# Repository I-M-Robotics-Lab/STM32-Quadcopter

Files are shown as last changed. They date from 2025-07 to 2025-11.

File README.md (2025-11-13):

# STM32-Quadcopter: Low-cost Quadcopter Design

### Description





**[Website](https://www.imroboticslab.com/releases)** | **[Documentation](https://www.imroboticslab.com/docs/stm32-quadcopter)**  | **[Community Discord](https://discord.com/invite/WJuUWsy6DJ)** | **[3D Models & Prints](https://makerworld.com/en/models/1695470-quadcopter-3d-printable-stm32-mcu#profileId-1797658)**

This is a quadcopter design based on the STM32F411CEU Blackpill flight controller. The flight controller is compatible with INAV 6.0 firmware. The flight controller uses an MPU6500 for inertial measurements and a BMP280 for altitude sensing, and also supports an optional GPS and magnetometer module.

The frame is composed mostly of 2D parts cut from carbon-fiber sheets. Alternatively, you can 3D-print parts in carbon-fiber-reinforced filaments (PET-CF, PAHT-CF, PA6-CF, PPS-CF), with less-critical components in ABS.

|  |
| --- |

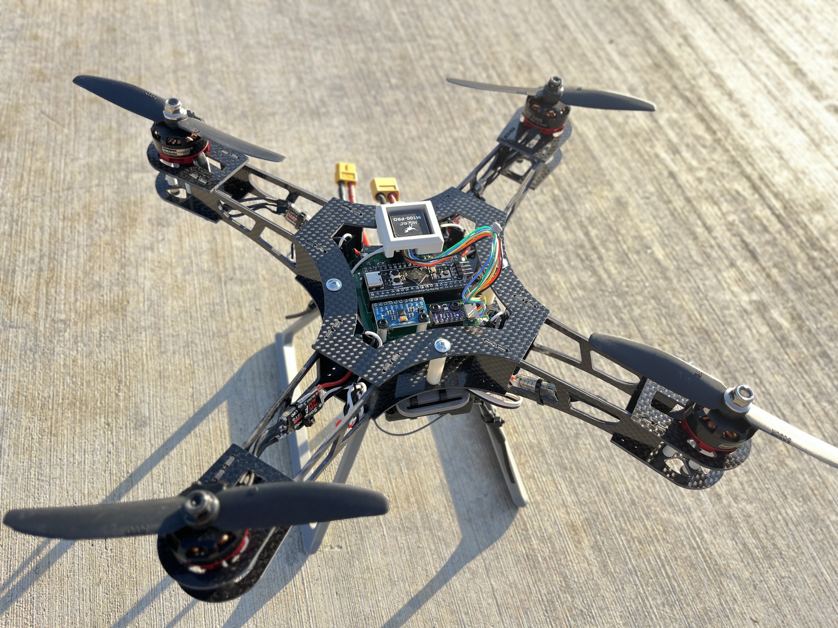
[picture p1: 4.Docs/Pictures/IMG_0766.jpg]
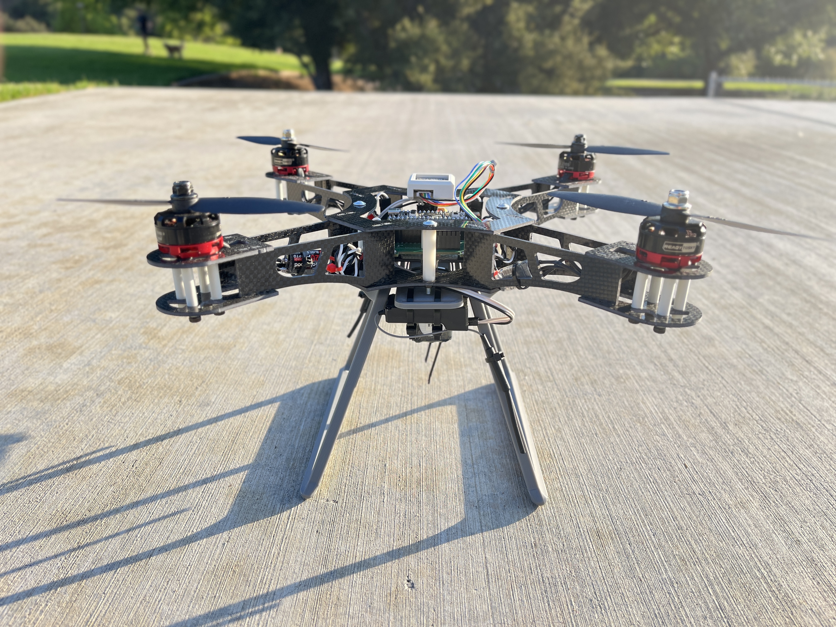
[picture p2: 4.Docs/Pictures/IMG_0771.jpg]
|  |  |
| --- | --- |

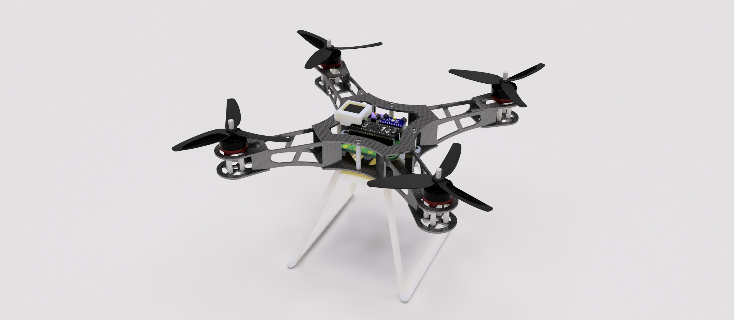
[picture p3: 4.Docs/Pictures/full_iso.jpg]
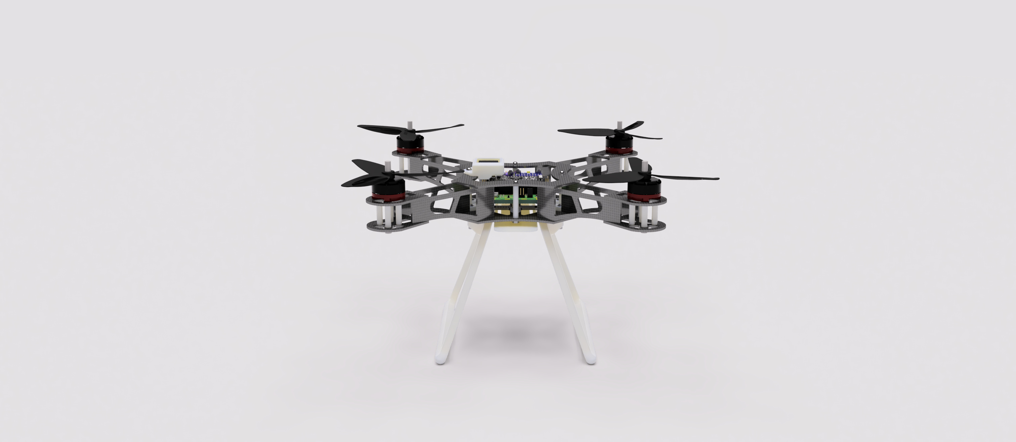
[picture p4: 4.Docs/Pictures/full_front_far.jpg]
Front view of frame
|  |  |
| --- | --- |

---

## Table of Contents

- [Introduction](#stm32-quadcopter-low-cost-quadcopter-design)
- [Frame](#frame)
  - [CF Components](#cf-components)
  - [ABS Components](#abs-components)
  - [Mechanical Components BOM](#mechanical-components-bom)
- [Electronics](#electronics)
  - [Electronics BOM](#electronics-bom)
  - [SMD Components](#smd-components)
  - [Pins](#pins)
  - [Sample Diagram](#sample-diagram)
  - [GPS (UART1) Wiring](#gps-uart1-wiring)
  - [Capacitor for Spike Filtering](#capacitor-for-spike-filtering)
- [Firmware](#firmware)
  - [Build](#build)
    - [Prerequisites](#prerequisites)
    - [Clone INAV](#clone-inav)
    - [Add Target](#add-target)
    - [Patch Code](#patch-code)
    - [Build](#build-1)
  - [Flash](#flash)
  - [MPU9250 Issue](#mpu9250-issue)
- [Configuration and Setting Up](#configuration-and-setting-up)

---

## Frame

Use the assembled CAD model in the `3.Models/` folder as a reference to build.

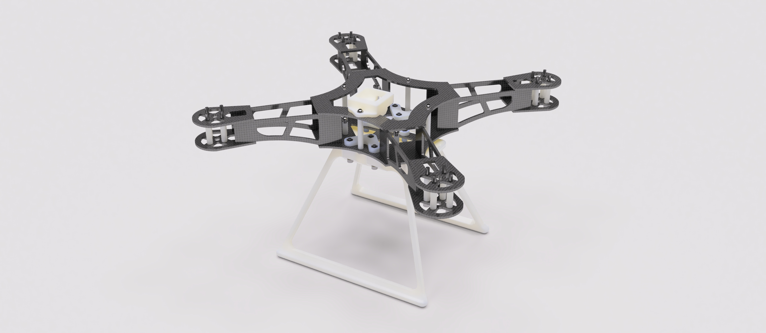
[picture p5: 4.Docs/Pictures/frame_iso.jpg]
Front view of frame


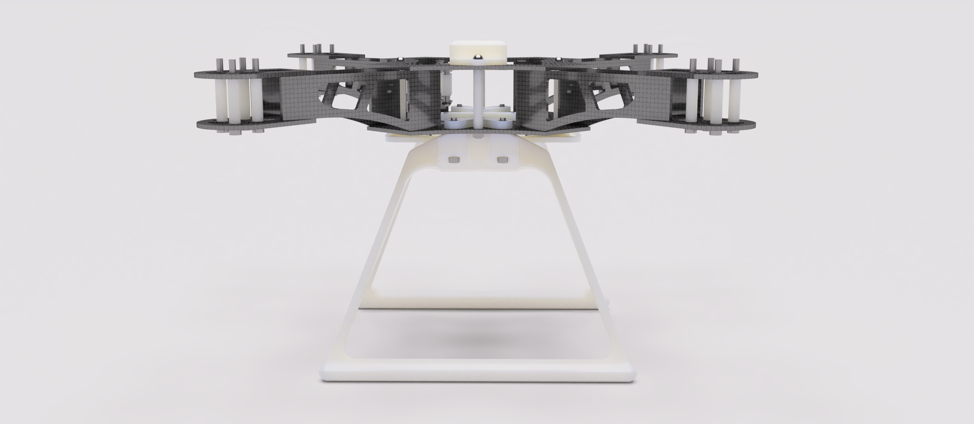
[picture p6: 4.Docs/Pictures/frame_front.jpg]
Front view of frame


### CF Components

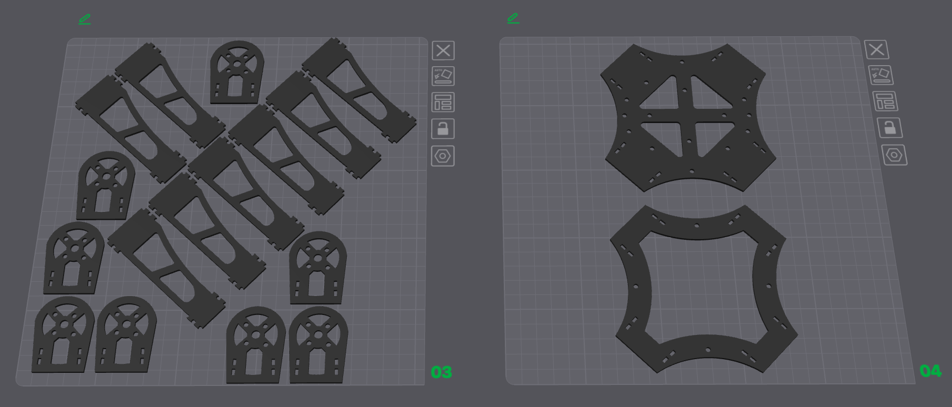
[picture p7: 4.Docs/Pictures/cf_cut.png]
CF cut patterns


*All files are under `3.Models/`. Add dogbones and tolerances for manufacturability.*

### ABS Components

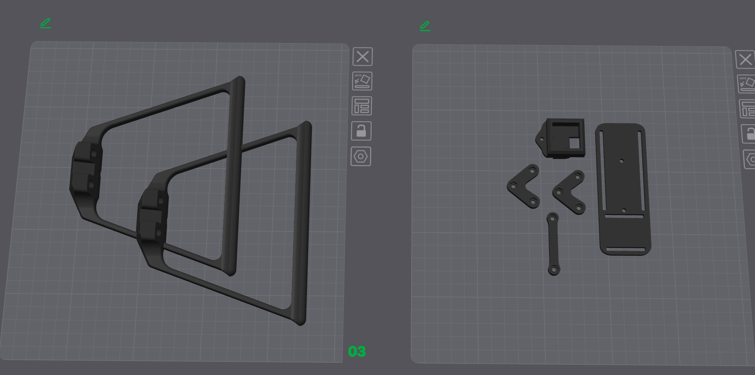
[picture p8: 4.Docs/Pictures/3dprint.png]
3D-printed ABS parts


*Recommend using a 0.4 mm or 0.6 mm high-strength print profile.*

**Mechanical Components BOM**

| Item Name | Qty |
|---|-----|
| M3 Hex Nut | 19  |
| M3 x 12mm Button Head Bolt | 2 |
| M3 x 20mm Button Head Bolt | 7 |
| M3 x 20mm Socket Head Bolt | 6 |
| M3 x 30mm Socket Head Bolt | 16  |
| M3 x 35mm Button Head Bolt | 3 |
| M3 x 40mm Button Head Bolt | 1 |
| Nylon Spacer 3-5-11.2 | 8 |
| Nylon Spacer 3-5-20 | 16  |
| Nylon Spacer 3-5-30 | 4 |
| Nylon Spacer 3-5-5 | 2 |

---
## Electronics

**Structure**
```text
1. Electronics/
  ├── Extra/
  │   ├── *.step
  │   └── ...
  ├── Hardware-backups/
  │   └── ...
  ├── Production/           ← Gerber output for fabrication
  │   ├── Hardware-B_Cu.gbl
  │   └── ...
  ├── Hardware.kicad_pcb    ← KiCAD PCB file
  ├── Hardware.kicad_sch    ← KiCAD Schematics file
  ├── Hardware.kicad_pro    ← KiCAD project
  ├── JLCPCB.kicad_dru      ← Rules for JLCPCB manufacturing
  ├── Production.zip        ← Gerber
  └── Schematics.pdf        ← Schematics
```

### Electronics BOM

| Component | Qty |
|---|:---:|
| RS2205 BLDC Motor | 4 |
| BLHeli_S 20A ESC | 4 |
| 5030R Propeller | 2 |
| STM32F411CEU6 “Blackpill” | 1 |
| MPU6500 / MPU9250 Module | 1 |
| BMP280 Module | 1 |
| 330 µF @ 50 V Capacitor | 1 |
| FS-iA6B Receiver | 1 |
| FS-iA6B Transmitter | 1 |
| Ovonic 1500 mAh 120C 3s Battery | 1 |
| XT60 Connector | 1 |

### SMD Components

Gerber files and BOM are available under the electronics folder.

### Pins

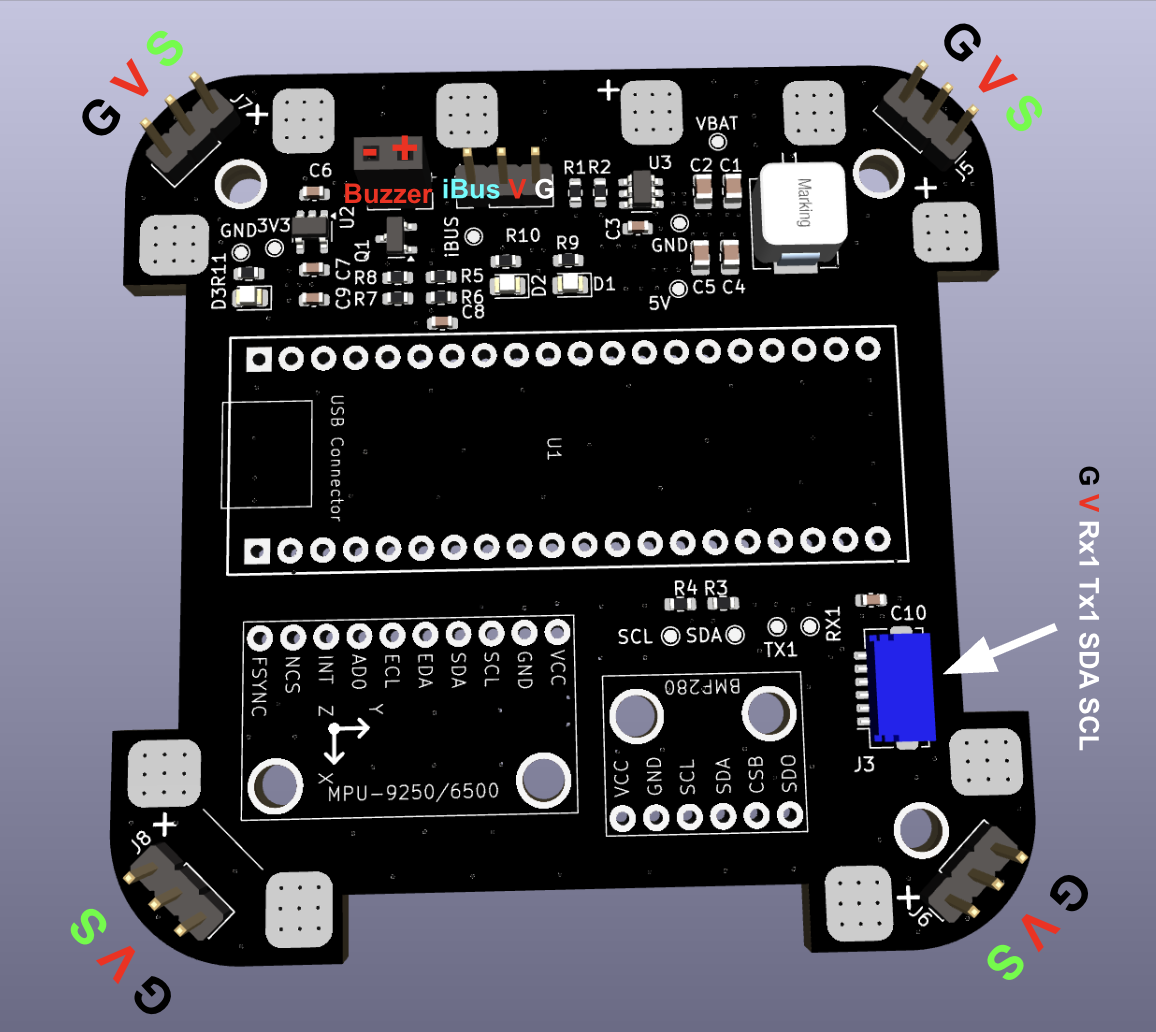
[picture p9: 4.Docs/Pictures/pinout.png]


### Sample Diagram

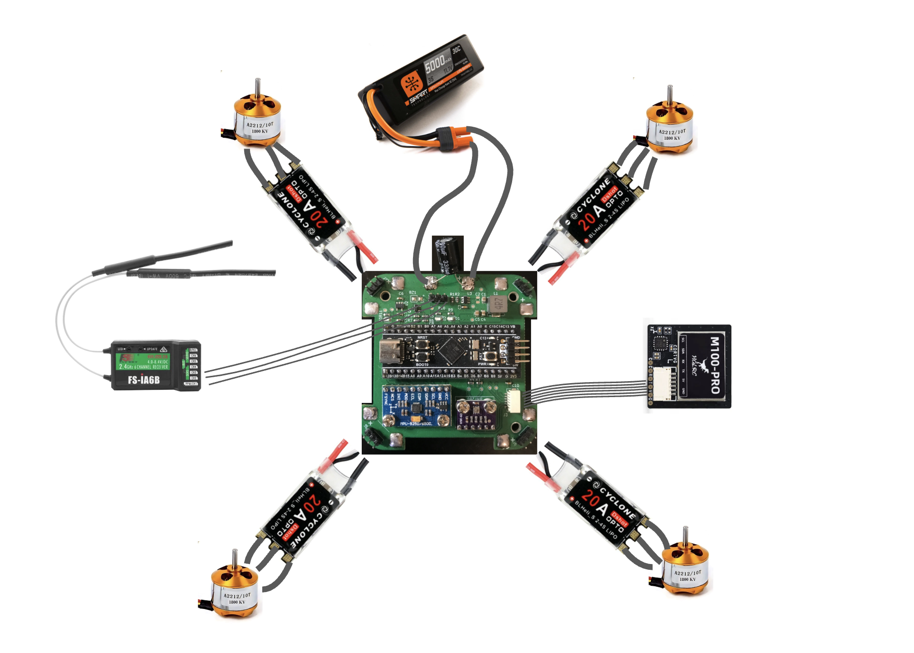
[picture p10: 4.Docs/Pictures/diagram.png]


*Diagram only; not actual wiring. Please follow the strict pin assignments.*

### GPS (UART1) Wiring

Ensure connectors are wired correctly according to the pinout. Note that RX should connect to TX: `RX1` → GPS `TX`, `TX1` → GPS `RX`.

### Capacitor for Spike Filtering

One or more bulk electrolytic capacitor is recommended to protect against voltage spikes. Use an electrolytic capacitor such as **330 µF @ 50 V** and place it between `VBAT` and `GND` near the input. For extra protection, a **TVS diode** clampeing at ~**12 V** is ideal.

---
## Firmware

### Build

The firmware used is **INAV v6.0.0 ([github link](https://github.com/iNavFlight/inav))**. This project does not support **INAV v7+** currently due to USB issue. If one wants to modify the target file or other configurations of the firmware, they must rebuild the binary. Follow this guide to build:

**Prerequisites**
- CMake ≥ 3.15  
- Ninja  
- gcc-arm-none-eabi toolchain 

**Clone INAV**
```shell
git clone https://github.com/iNavFlight/inav.git
cd inav
git checkout 6.0
```

**Add Target**

Copy the entire `2.Firmware/GYW_BLACKPILL_F411` folder into the local INAV repository under `src/main/target/` so that it ends up as:

```text
inav/
└── src/
    └── main/
        └── target/
            ├──  GYW_BLACKPILL_F411/
            └── ...
```

**Patch Code**

INAV 6.0 doesn’t support a **25 MHz HSE clock** by default, so if your board (like the **Blackpill F411**) uses a 25 MHz crystal, you must update the PLL setup in `src/main/target/system_stm32f4xx.c` as follows:

In `system_stm32f4xx.c`, locate the PLL setup region and modify it as follows:
```diff
#if defined(STM32F40_41xxx) || defined(STM32F427_437xx) || defined(STM32F429_439xx) || defined(STM32F401xx) || defined(STM32F469_479xx) || defined(STM32F446xx) || defined(STM32F410xx) || defined(STM32F411xE)
+   #if HSE_VALUE == 25000000
+       #define PLL_M   25
+   #elif HSE_VALUE == 24000000
-   #if HSE_VALUE == 24000000
        #define PLL_M   24
    #elif HSE_VALUE == 16000000
        #define PLL_M   16
    #elif HSE_VALUE == 8000000
        #define PLL_M   8
    #else
        #error Invalid HSE_VALUE
    #endif
#else
    #error Undefined CPU
#endif
```

**Build**

Ensure that you have installed all dependencies. Inside the inav root repository execute:
```shell
mkdir -p build && cd build
cmake .. -G Ninja \
  -DBOARD=GYW_BLACKPILL_F411 \
  -DCMAKE_TOOLCHAIN_FILE=../tools/cmake/toolchain-arm-none-eabi.cmake
ninja
```

The firmware binary should be at `build/inav_6.0.0_GYW_BLACKPILL_F411.hex`.

### Flash

First, download the **INAV Configurator v6.0.0** from [this link](https://github.com/iNavFlight/inav-configurator/releases/tag/6.0.0). Once installed, launch INAV Configurator and connect to the Blackpill via USB. Cut the **red wire** in the USB cable to prevent it from powering the Blackpill. Instead, power the flight controller using an external **3S battery**.

<div style="text-align: center;">
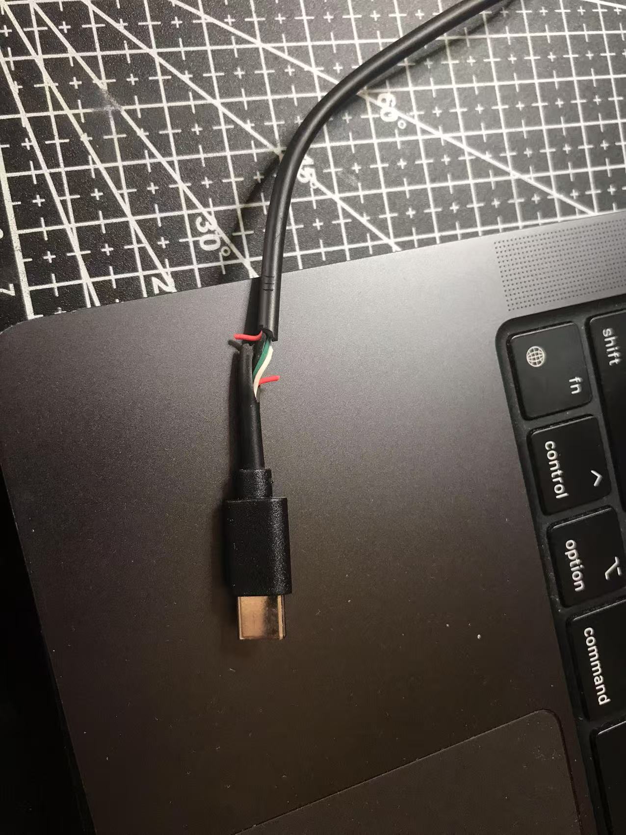
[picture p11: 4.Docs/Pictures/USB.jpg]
USB
  
</div>

To enter DFU mode, hold the **BOOT** button on the Blackpill while powering it on. Alternatively, you can press **RESET** while holding the BOOT button. When in DFU mode, the blue LED on the Blackpill will be off, and the board should appear in the INAV Configurator’s drop-down menu as a DFU device. Move to the **Firmware Flasher** tab on the left. Click **Load Firmware**, select the file `inav_6.0.0_GYW_BLACKPILL_F411.hex` (found in the `firmware` folder), then click **Flash Firmware**.

<div style="text-align: center;">
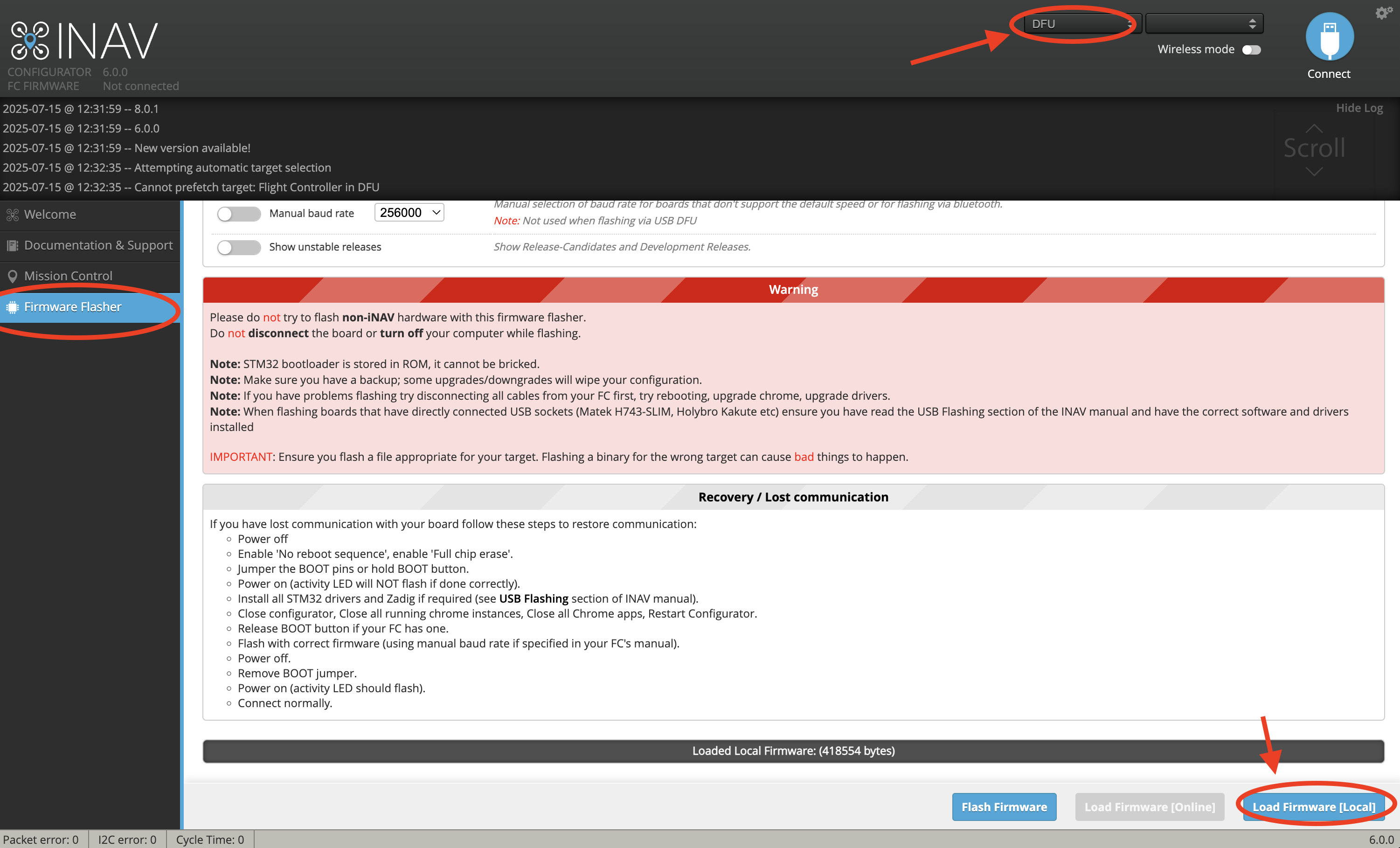
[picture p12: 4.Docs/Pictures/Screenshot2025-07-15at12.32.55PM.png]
  
</div>

A progress bar will appear during firmware flash.

<div style="text-align: center;">
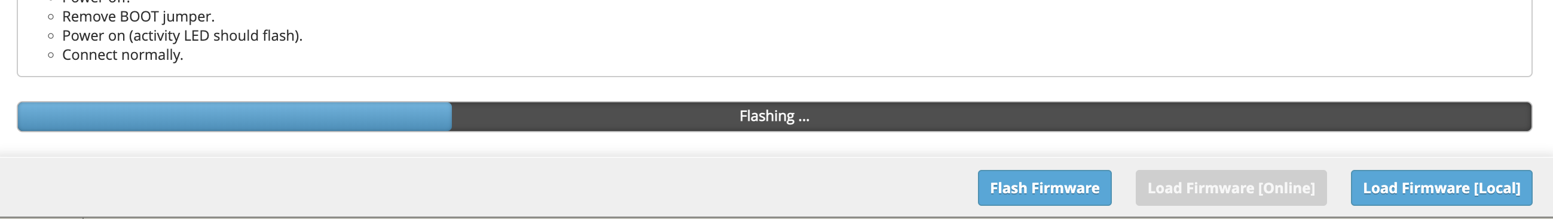
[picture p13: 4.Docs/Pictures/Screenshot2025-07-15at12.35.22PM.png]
  
</div>

When the firmware is successfully flashed, click connect. The configuration menu should show up. 
<div style="text-align: center;">
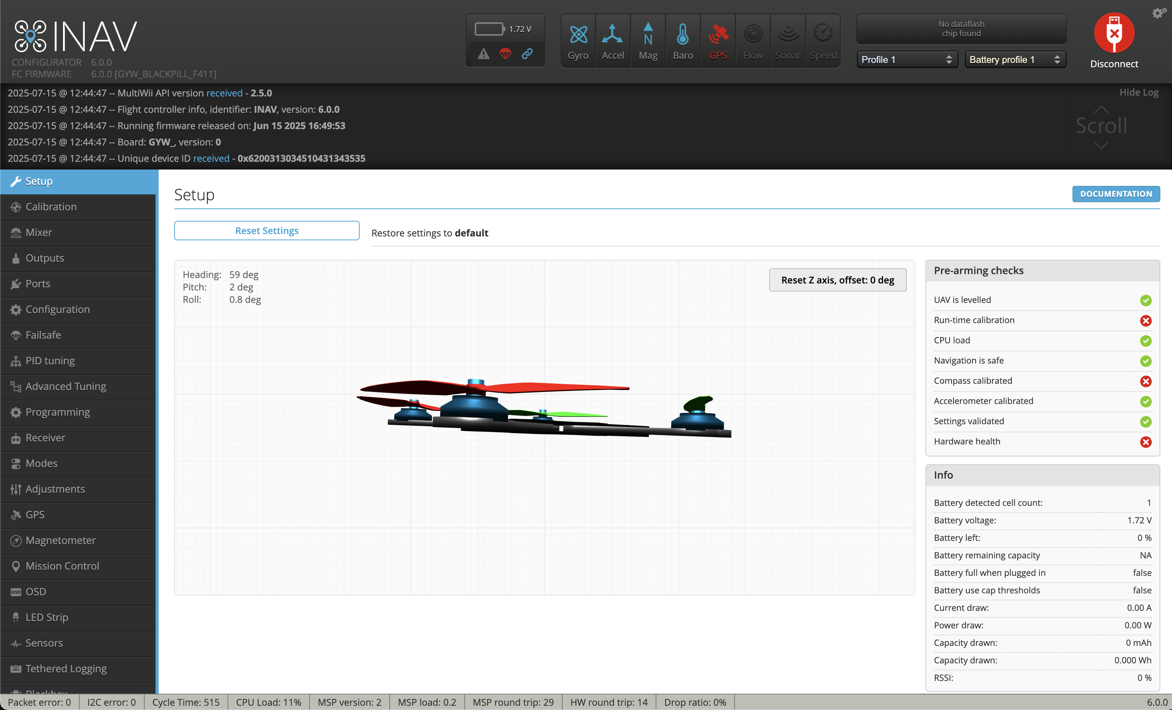
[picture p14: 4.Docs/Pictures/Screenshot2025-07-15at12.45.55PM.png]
  
</div>

### MPU9250 Issue

If you are using a MPU9250 module, you may encounter the problem that INAV does not recognize the accelerometer. This is due to many boards labeled MPU9250 actually house only an **MPU6500** (omitting or substituting the magnetometer). Since drones often use an external magnetometer, this usually isn’t critical if your accelerometer and gyro (MPU6500) work. 

To identify your chip, read the `WHO_AM_I` register (`0x75`) via I²C (use an Arduino or something similar to do this part). Example Arduino code:
```cpp
#include <Wire.h>
const uint8_t MPU_ADDR     = 0x68; // I²C address
const uint8_t WHO_AM_I_REG = 0x75;
void setup() {
  Serial.begin(115200);
  Wire.begin();
  delay(100);
  Wire.beginTransmission(MPU_ADDR);
  Wire.write(WHO_AM_I_REG);
  if (Wire.endTransmission(false) != 0) {
    Serial.println(F("no device found")); while (1);
  }
  Wire.requestFrom(MPU_ADDR, (uint8_t)1);
  if (Wire.available()) {
    uint8_t id = Wire.read();
    Serial.print(F("WHO_AM_I = 0x"));
    Serial.println(id, HEX);
  } else {
    Serial.println(F("no data returned"));
  }
}
```
If it prints `0x71`, it’s MPU6500; `0x73` indicates MPU9250. 

The current binary file and target is configured for **MPU6500**. To use MPU9250, comment out the block for MPU6500 and uncomment the MPU9250 block in the target file. Rebuild the binary and flash. It looks like this:

```c
#define USE_IMU_MPU9250
#define IMU_MPU9250_ALIGN   CW0_DEG
#define MPU9250_CS_PIN      PB12
#define MPU9250_SPI_BUS     BUS_SPI2
```

---
## Configuration and Setting Up

Follow standard inav configuration procedures.

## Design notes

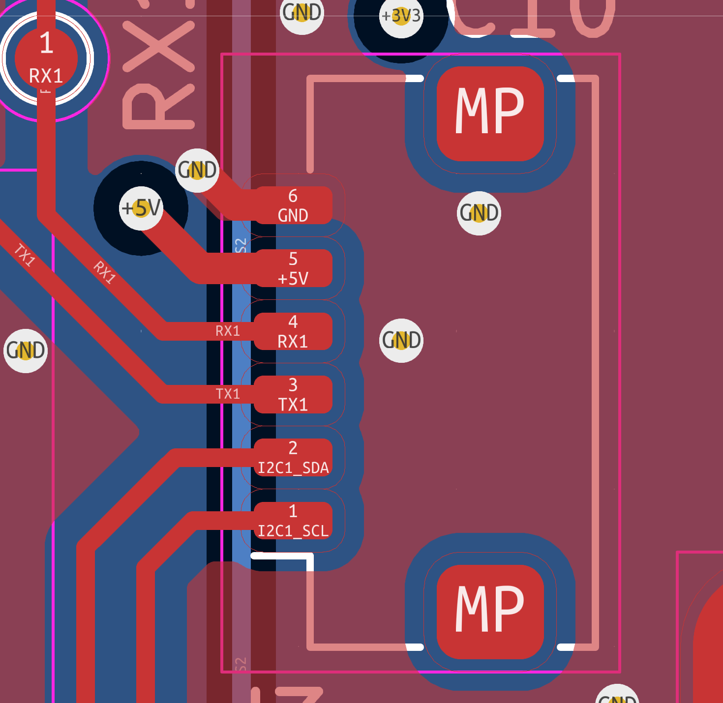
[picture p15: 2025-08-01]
4.Docs/Pictures/pcb_uart.png

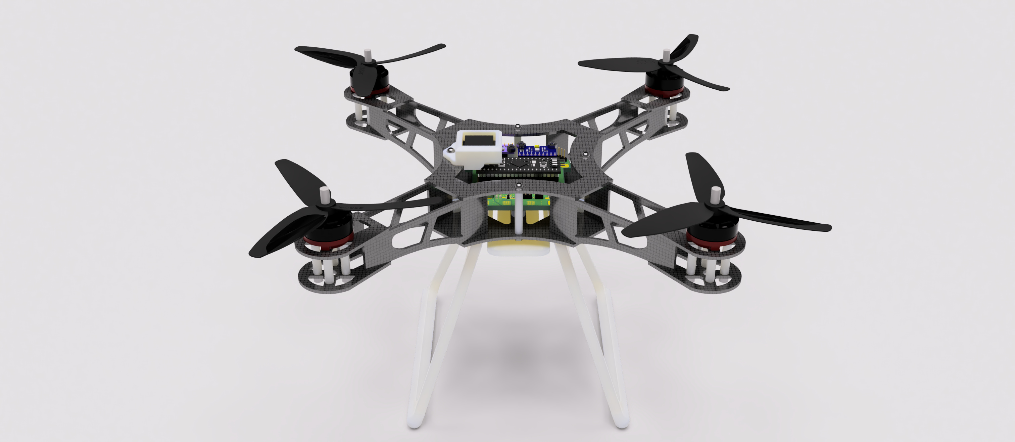
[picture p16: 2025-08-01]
4.Docs/Pictures/full_front.jpg

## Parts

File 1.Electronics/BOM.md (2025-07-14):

| Reference | Value | Package | Qty |
|---|---|---|-----|
| C1 | 10u 25V | 0805 | 1 |
| C2 | 0.1u 25V | 0805 | 1 |
| C3,C8,C9,C10 | 0.1u 10V | 0603 | 4 |
| C4 | 22u  16V | 0805 | 1 |
| C5 | 22u 16V | 0805 | 1 |
| C6,C7 | 1uF 10V | 0603 | 2 |
| R1 | 54.9k | 0603 | 1 |
| R2,R6,R8 | 10k | 0603 | 3 |
| R3,R4 | 4.7k | 0603 | 2 |
| R5 | 33k | 0603 | 1 |
| R7 | 100 | 0603 | 1 |
| R9,R10,R11 | 470 | 0603 | 3 |
| D1 | RED | 0805 LED | 1 |
| D2 | GREEN | 0805 LED | 1 |
| D3 | BLUE | 0805 LED | 1 |
| L1 | 4.7u | 7050 Inductor | 1 |
| Q1 | IRLML6344  | SOT-23 | 1 |
| U2 | TLV73333P  | SOT-23-5 | 1 |
| U3 | TPS563200  | SOT-23-6 | 1 |
| U1 | STM32F411CEU1_Pins | STM32F411 Module  | 1 |
| J1 | MPU9250_Pins | MPU9250 Module | 1 |
| J2 | BMP280_Pins | BMP280 Module | 1 |
| J3 | JST 6p | JST SH 6P 1.0mm Horiz | 1  |
| J4 | Pin Header 1x3 | Pin Header 1x3 2.54mm| 1 |
| J5 | Pin Header 1x3 | Pin Header 1x3 2.54mm| 1 |
| J6 | Pin Header 1x3 | Pin Header 1x3 2.54mm| 1 |
| J7 | Pin Header 1x3 | Pin Header 1x3 2.54mm| 1 |
| J8 | Pin Header 1x3 | Pin Header 1x3 2.54mm| 1 |

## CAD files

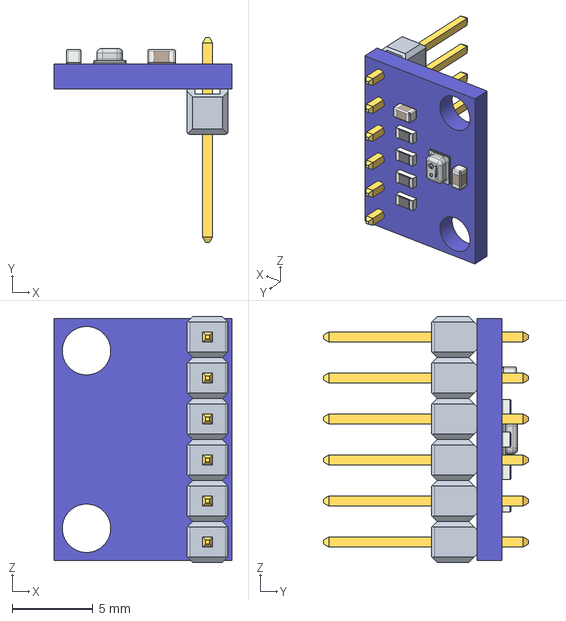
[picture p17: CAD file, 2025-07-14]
1.Electronics/Extra/bmp280_module.stp
11.0 x 12.7 x 15.2 mm

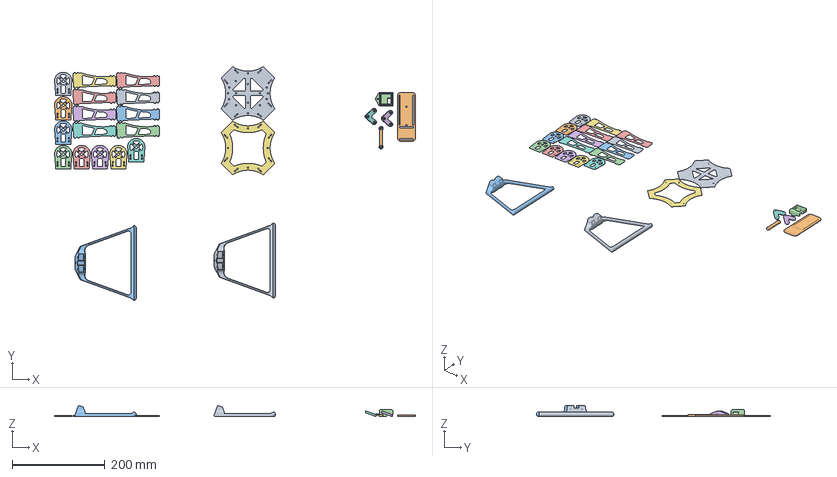
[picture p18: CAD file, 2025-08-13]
3.Models/All_on_one_plate.3mf
779.0 x 505.1 x 24.1 mm
Bottom_Plate v4.step
Battery_Plate v3.step
Leg1 v41.step x 2
GPS_mount v1.step
arm_plate_1 v17.step x 8
leg_hold v4.step x 2
Top_Plate v2.step
bat_hold v2.step
motor_plate_up_1 v9.step x 8

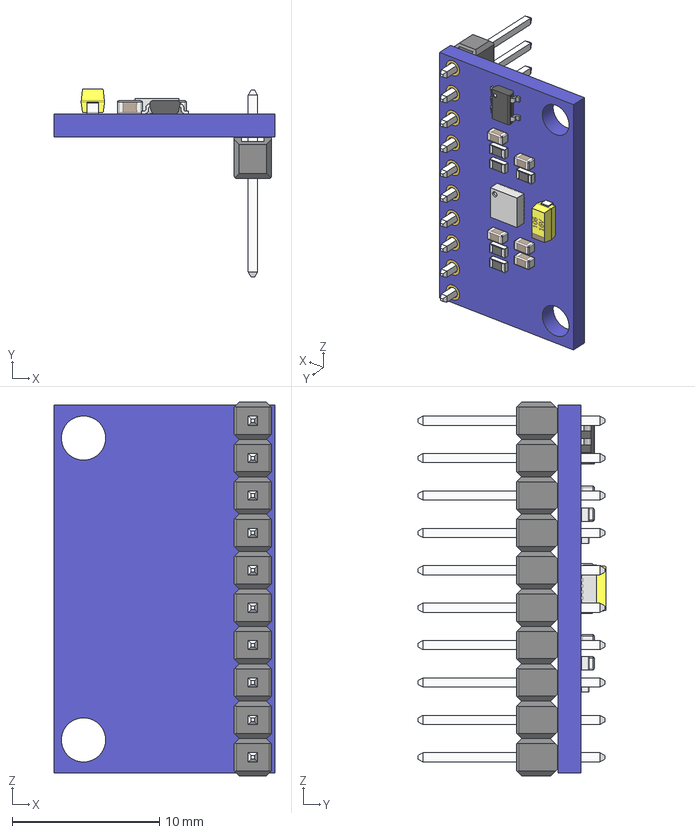
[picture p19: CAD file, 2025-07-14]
1.Electronics/Extra/MPU-9250.stp
15.0 x 12.8 x 25.4 mm
board
hole_plating x 20
Pin Header 1x10 TH Pitch 2.54mm
MPU-9250_1
tantalum 10uF
SOT23_5
RESC-0603 x 5
CAPC-0603-T0.9-BN x 5

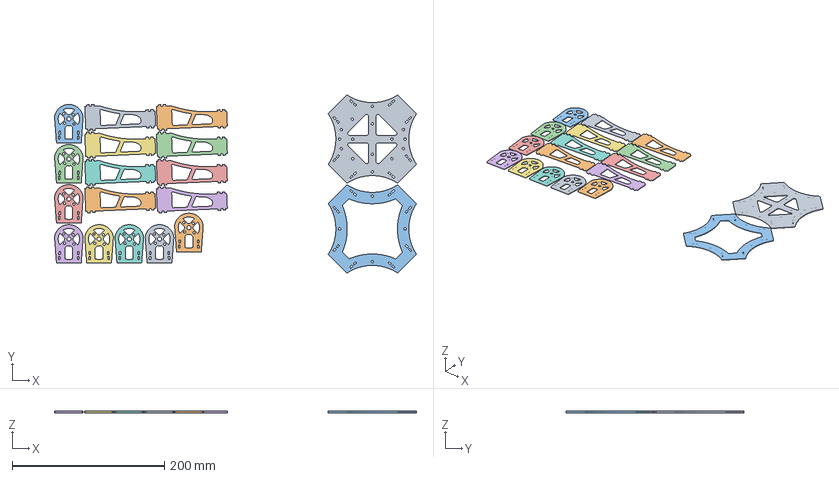
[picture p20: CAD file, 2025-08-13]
3.Models/CF_prints.3mf
475.4 x 233.9 x 2.00 mm
Bottom_Plate v4.step
arm_plate_1 v17.step x 8
Top_Plate v2.step
motor_plate_up_1 v9.step x 8

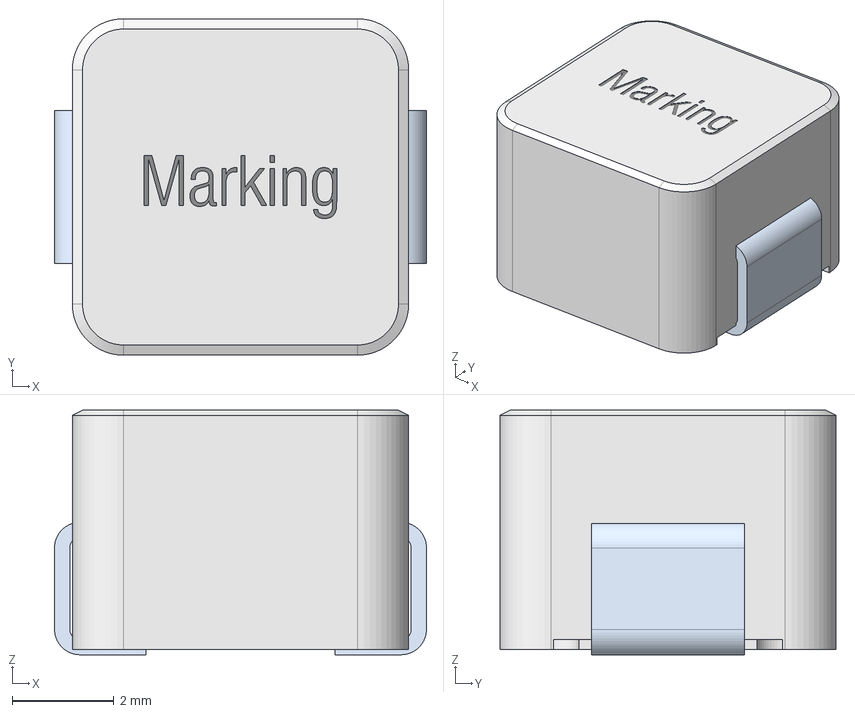
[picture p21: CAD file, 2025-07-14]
1.Electronics/Extra/WE-LHMI_7050LHMI+(rev1).stp
7.30 x 6.60 x 4.80 mm

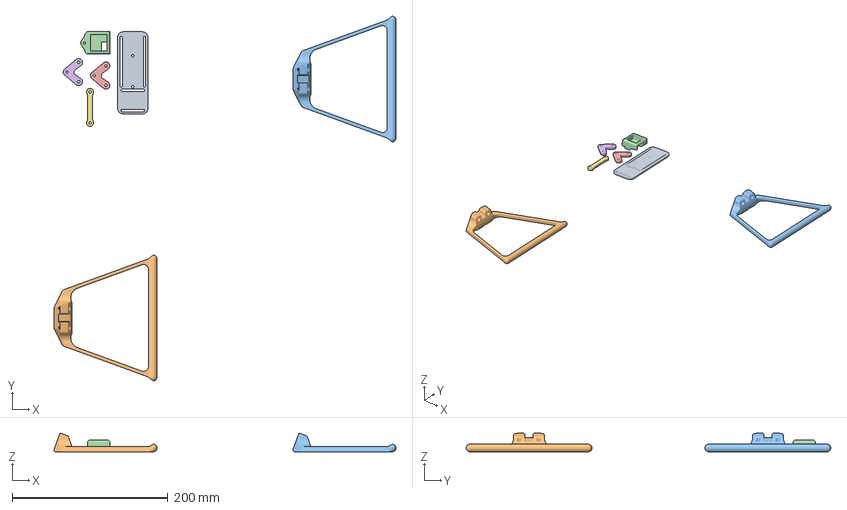
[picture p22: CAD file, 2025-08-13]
3.Models/ABS_print.3mf
439.8 x 469.1 x 24.1 mm
Battery_Plate v3.step
Leg1 v41.step x 2
GPS_mount v1.step
leg_hold v4.step x 2
bat_hold v2.step

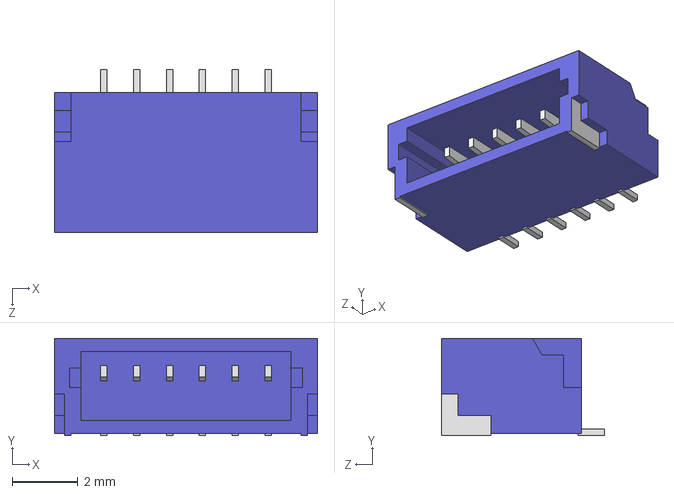
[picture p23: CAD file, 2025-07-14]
1.Electronics/Extra/SM06B-SRSS-TB.STEP
8.00 x 2.96 x 4.95 mm

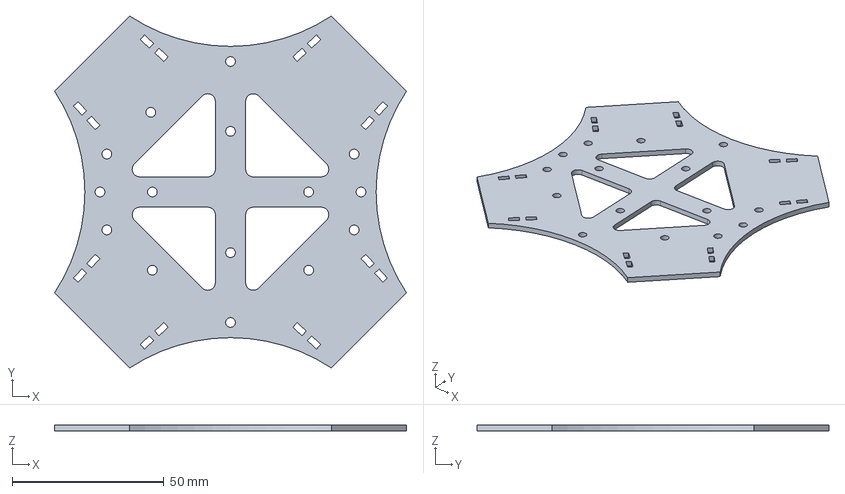
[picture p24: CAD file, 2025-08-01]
3.Models/Bottom_Plate v4.step
116.0 x 116.0 x 2.00 mm

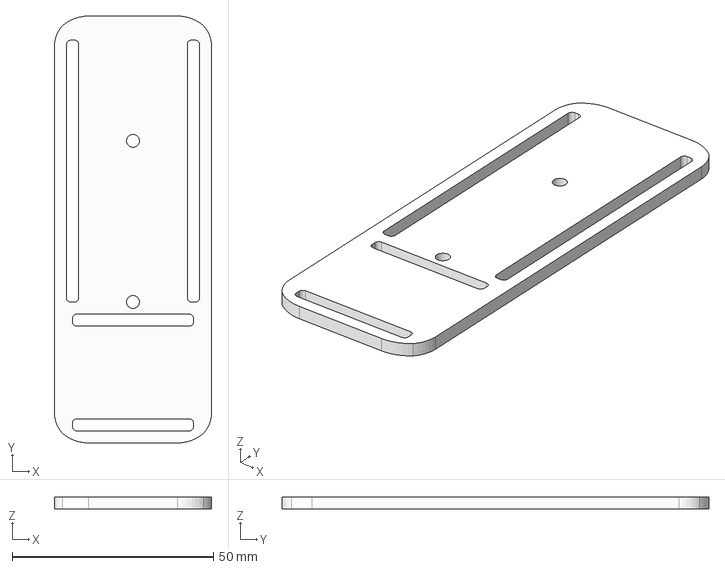
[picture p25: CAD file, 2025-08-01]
3.Models/Battery_Plate v3.step
39.0 x 106.0 x 3.00 mm

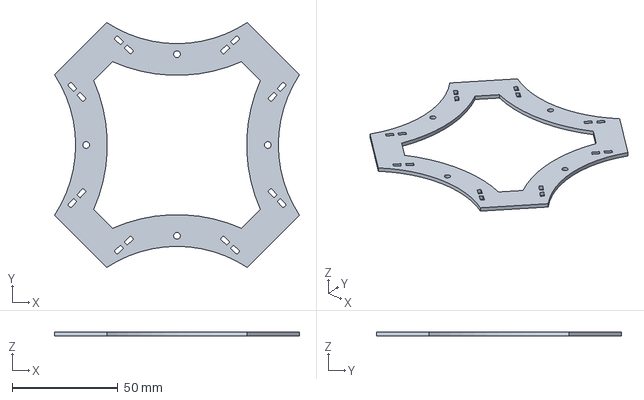
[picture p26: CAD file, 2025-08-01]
3.Models/Top_Plate v2.step
116.0 x 116.0 x 2.00 mm

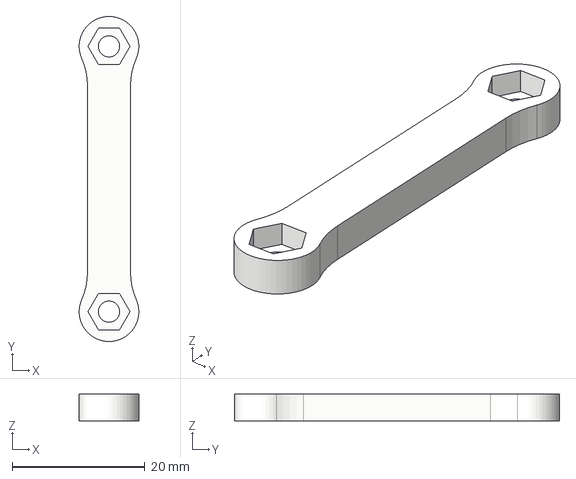
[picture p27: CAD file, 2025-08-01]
3.Models/bat_hold v2.step
8.99 x 49.0 x 4.00 mm

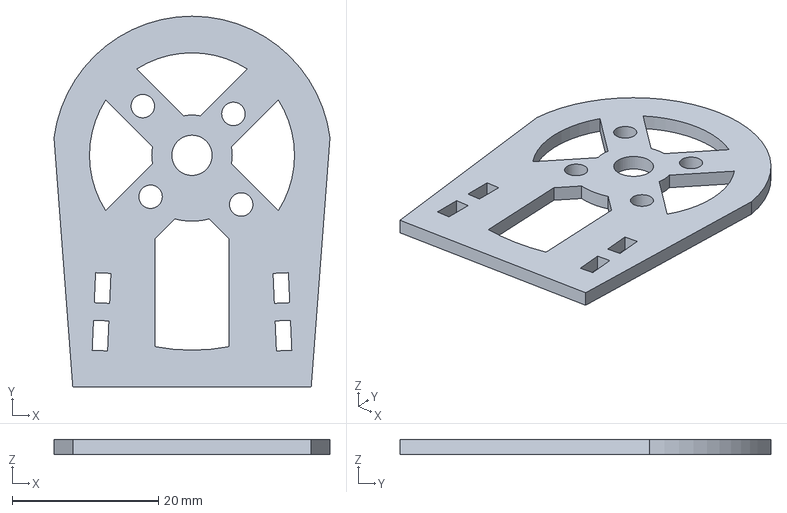
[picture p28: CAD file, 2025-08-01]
3.Models/motor_plate_up_1 v9.step
37.7 x 50.6 x 2.00 mm

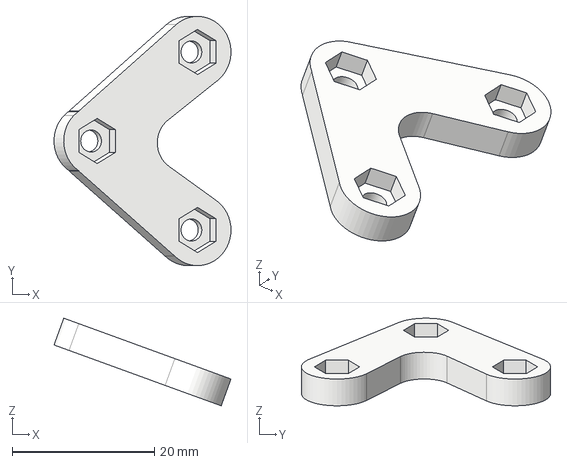
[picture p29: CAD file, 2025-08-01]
3.Models/leg_hold v4.step
24.9 x 35.0 x 12.3 mm

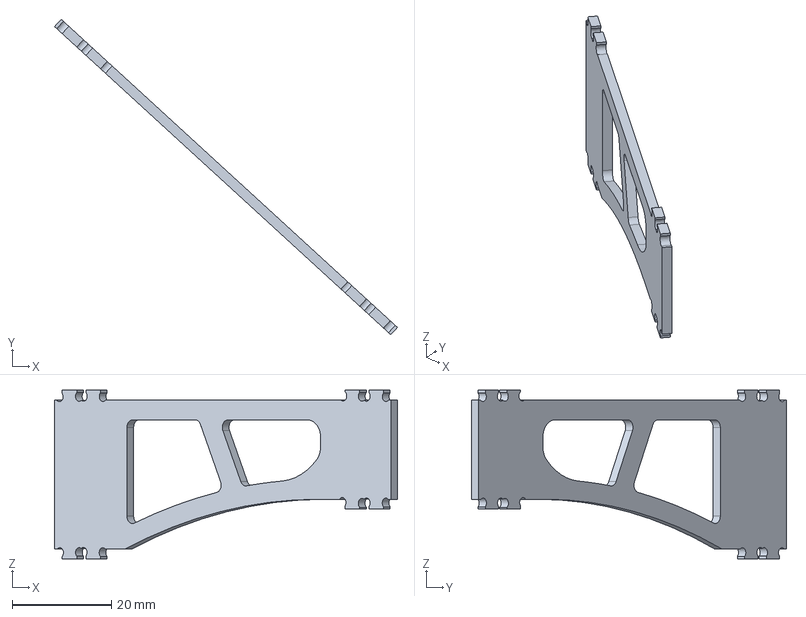
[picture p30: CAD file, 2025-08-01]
3.Models/arm_plate_1 v17.step
69.2 x 63.6 x 34.0 mm

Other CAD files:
3.Models/Leg1 v41.step
3.Models/GPS_mount v1.step

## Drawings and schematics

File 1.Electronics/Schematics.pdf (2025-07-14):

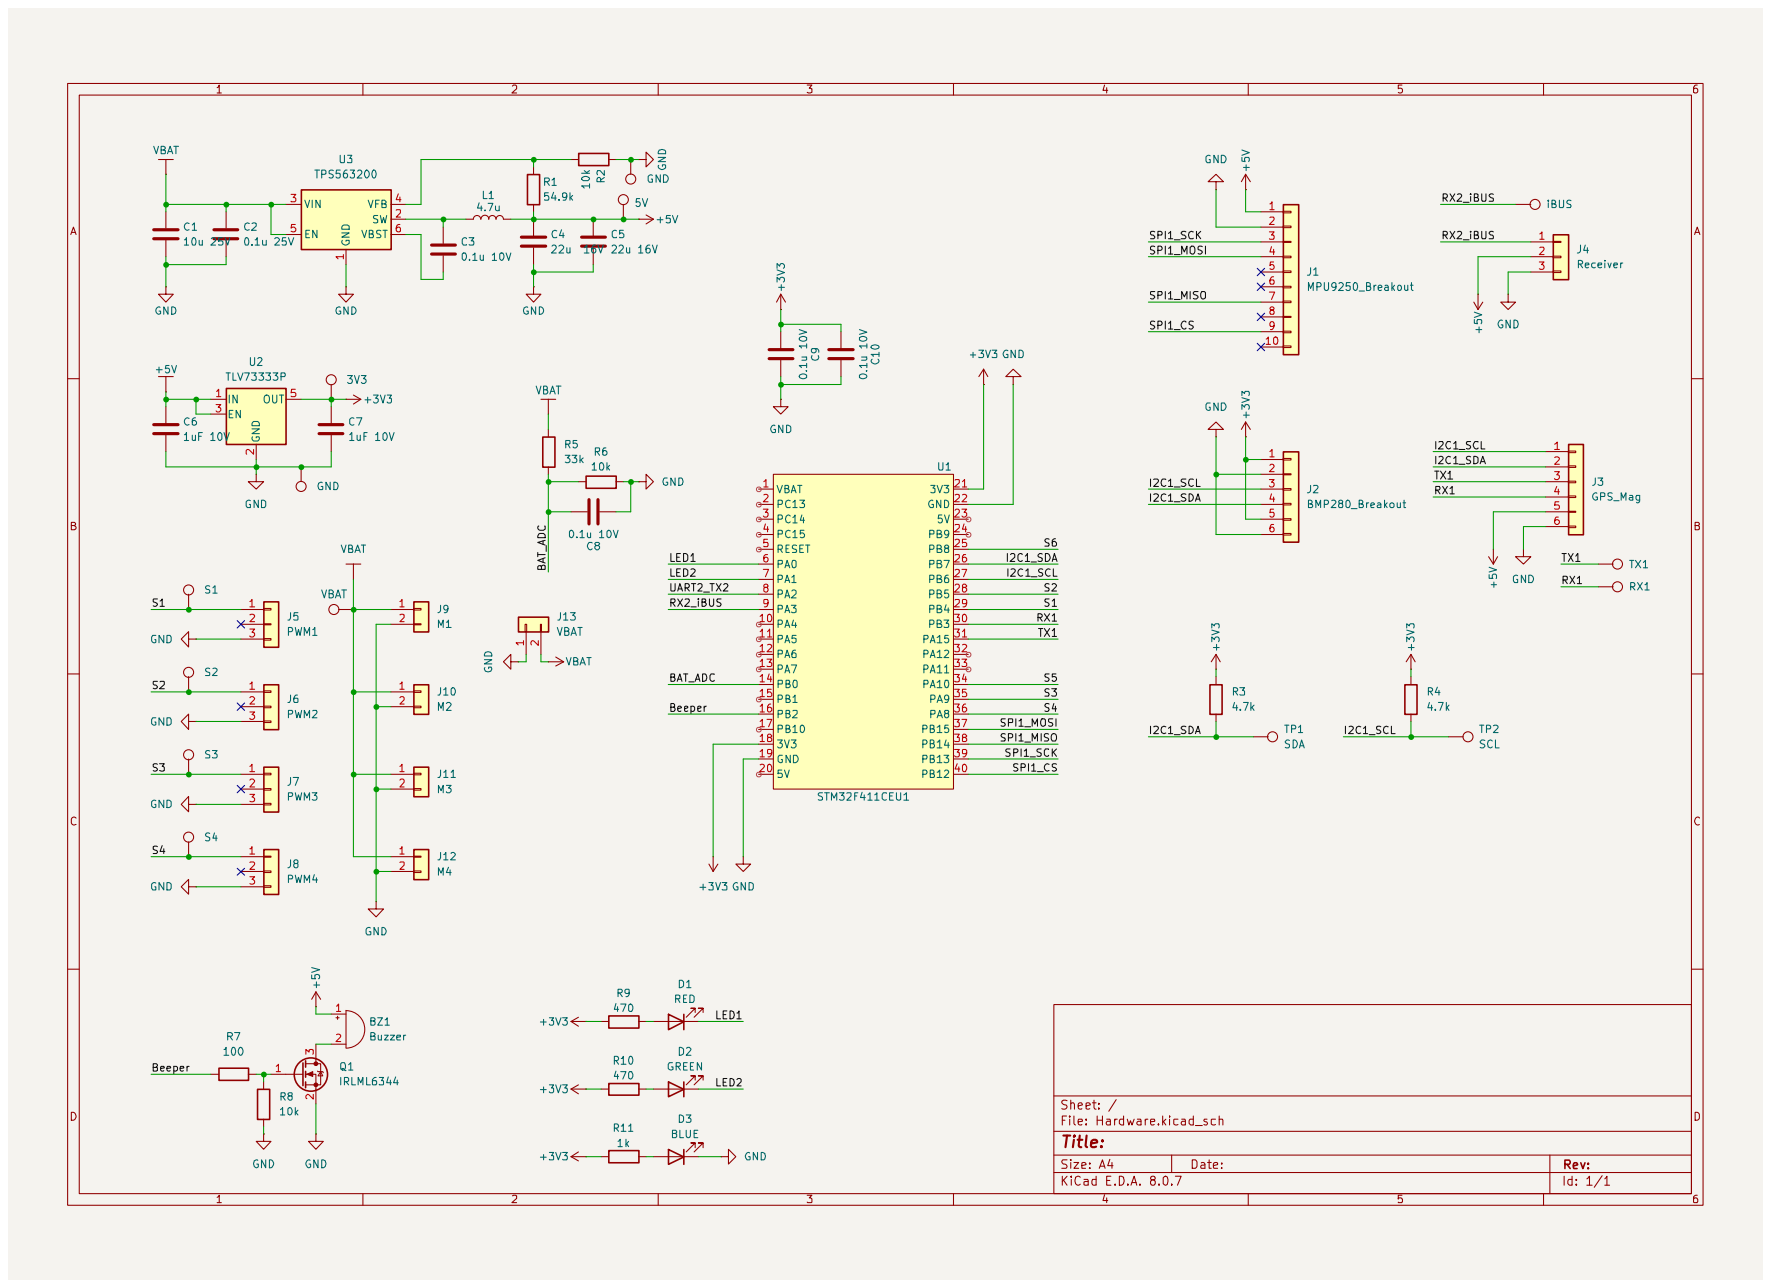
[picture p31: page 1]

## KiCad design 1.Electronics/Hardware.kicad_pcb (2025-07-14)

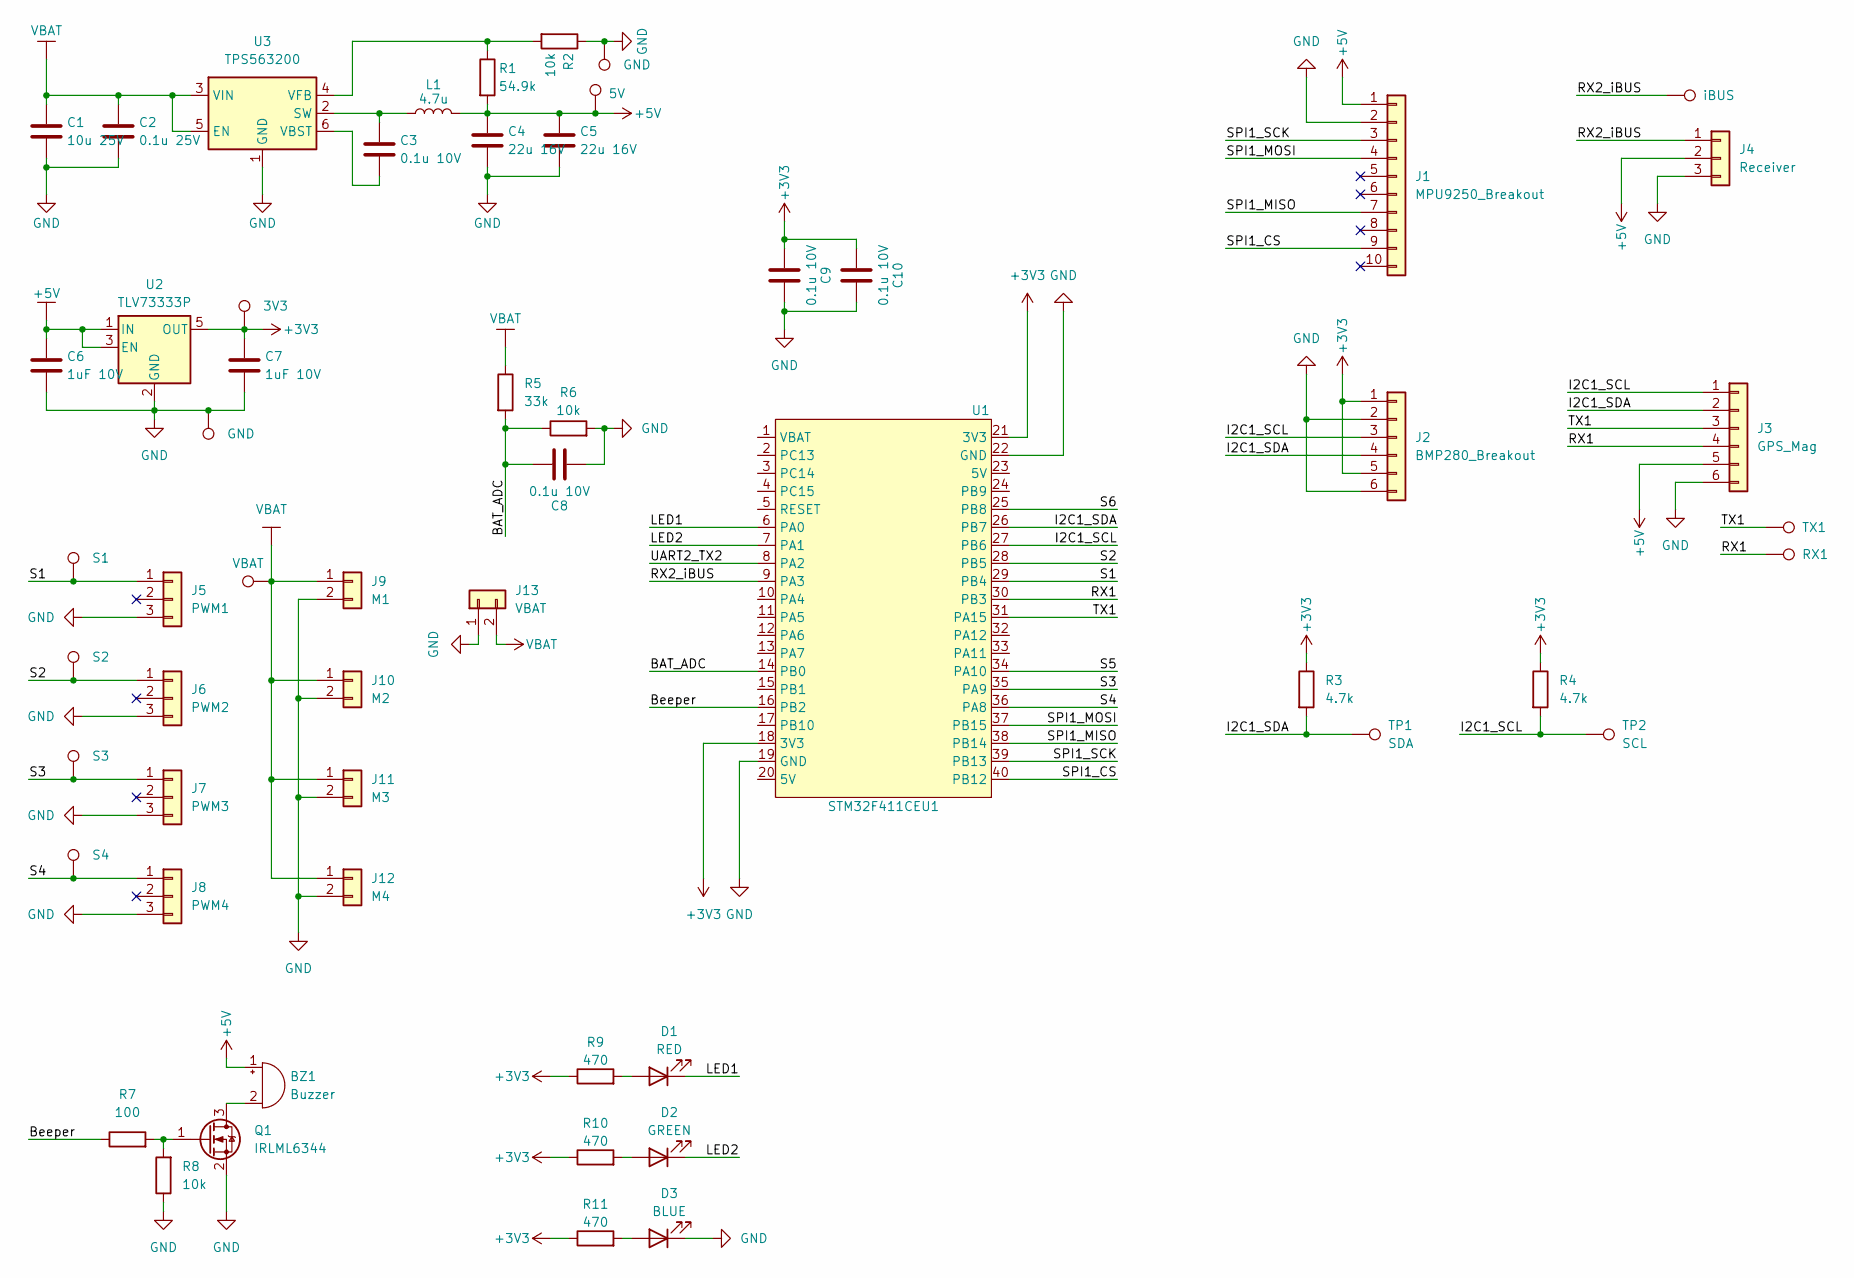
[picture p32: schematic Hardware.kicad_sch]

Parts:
BZ1: Buzzer; PinSocket_1x02_P2.54mm_Vertical
C1: 10u 25V; C_0805_2012Metric
C2: 0.1u 25V; C_0805_2012Metric
C3, C8, C9, C10: 0.1u 10V; C_0603_1608Metric
C4, C5: 22u 16V; C_0805_2012Metric
C6, C7: 1uF 10V; C_0603_1608Metric
D1: RED; LED_0805_2012Metric
D2: GREEN; LED_0805_2012Metric
D3: BLUE; LED_0805_2012Metric
J1: MPU9250_Breakout; MPU9250_Mod
J2: BMP280_Breakout; BMP280_Mod
J3: GPS_Mag; JST_SHL_SM06B-SHLS-TF_1x06-1MP_P1.00mm_Horizontal
J4: Receiver; PinHeader_1x03_P2.54mm_Vertical
J5: PWM1; PinHeader_1x03_P2.54mm_Vertical
J6: PWM2; PinHeader_1x03_P2.54mm_Vertical
J7: PWM3; PinHeader_1x03_P2.54mm_Vertical
J8: PWM4; PinHeader_1x03_P2.54mm_Vertical
J9: M1; PAD_1x02_5mm
J10: M2; PAD_1x02_5mm
J11: M3; PAD_1x02_5mm
J12: M4; PAD_1x02_5mm
J13: VBAT; PAD_1x02_5mm
L1: 4.7u; L_Wurth_WE-LHMI-7050
Q1: IRLML6344; SOT-23
R1: 54.9k; R_0603_1608Metric
R2, R6, R8: 10k; R_0603_1608Metric
R3, R4: 4.7k; R_0603_1608Metric
R5: 33k; R_0603_1608Metric
R7: 100; R_0603_1608Metric
R9, R10, R11: 470; R_0603_1608Metric
TP1: SDA; TestPoint_Pad_D1.0mm
TP2: SCL; TestPoint_Pad_D1.0mm
TP3: 5V; TestPoint_Pad_D1.0mm
TP4, TP6: GND; TestPoint_Pad_D1.0mm
TP5: 3V3; TestPoint_Pad_D1.0mm
TP7: TX1; TestPoint_Pad_D1.0mm
TP8: RX1; TestPoint_Pad_D1.0mm
TP9: iBUS; TestPoint_Pad_D1.0mm
TP10: S1; TestPoint_Pad_D1.0mm
TP11: S2; TestPoint_Pad_D1.0mm
TP12: S3; TestPoint_Pad_D1.0mm
TP13: S4; TestPoint_Pad_D1.0mm
TP14: VBAT; TestPoint_Pad_D1.0mm
U1: STM32F411CEU1; Stm32f411ceu_module
U2: TLV73333P; SOT-23-5
U3: TPS563200; SOT-23-6

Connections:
+3V3: C7.1, C9.2, C10.2, J2.1, J2.5, R3.1, R4.1, R9.1, R10.1, R11.1, TP5.1, U1.18 (3V3), U1.21 (3V3), U2.5 (OUT)
+5V: BZ1.1 (+), C4.1, C5.1, C6.1, J1.1, J3.5, J4.2, L1.2, R1.2, TP3.1, U2.1 (IN), U2.3 (EN)
/BAT_ADC: C8.1, R5.2, R6.1, U1.14 (PB0)
/Beeper: R7.1, U1.16 (PB2)
/I2C1_SCL: J2.3, J3.1, R4.2, TP2.1, U1.27 (PB6)
/I2C1_SDA: J2.4, J3.2, R3.2, TP1.1, U1.26 (PB7)
/LED1: D1.1 (K), U1.6 (PA0)
/LED2: D2.1 (K), U1.7 (PA1)
/RX1: J3.4, TP8.1, U1.30 (PB3)
/RX2_iBUS: J4.1, TP9.1, U1.9 (PA3)
/S1: J5.1, TP10.1, U1.29 (PB4)
/S2: J6.1, TP11.1, U1.28 (PB5)
/S3: J7.1, TP12.1, U1.35 (PA9)
/S4: J8.1, TP13.1, U1.36 (PA8)
/S5: U1.34 (PA10)
/S6: U1.25 (PB8)
/SPI1_CS: J1.9, U1.40 (PB12)
/SPI1_MISO: J1.7, U1.38 (PB14)
/SPI1_MOSI: J1.4, U1.37 (PB15)
/SPI1_SCK: J1.3, U1.39 (PB13)
/TX1: J3.3, TP7.1, U1.31 (PA15)
/UART2_TX2: U1.8 (PA2)
GND: C1.2, C2.2, C4.2, C5.2, C6.2, C7.2, C8.2, C9.1, C10.1, D3.1 (K), J1.2, J2.2, J2.6, J3.6, J4.3, J5.3, J6.3, J7.3, J8.3, J9.2, J10.2, J11.2, J12.2, J13.1, Q1.2 (S), R2.1, R6.2, R8.1, TP4.1, TP6.1, U1.19 (GND), U1.22 (GND), U2.2 (GND), U3.1 (GND)
unnamed: BZ1.2 (-), Q1.3 (D)
unnamed: D1.2 (A), R9.2
unnamed: D2.2 (A), R10.2
unnamed: D3.2 (A), R11.2
unnamed: Q1.1 (G), R7.2, R8.2
unnamed: C3.1, L1.1, U3.2 (SW)
unnamed: C3.2, U3.6 (VBST)
unnamed: R1.1, R2.2, U3.4 (VFB)
VBAT: C1.1, C2.1, J9.1, J10.1, J11.1, J12.1, J13.2, R5.1, TP14.1, U3.3 (VIN), U3.5 (EN)

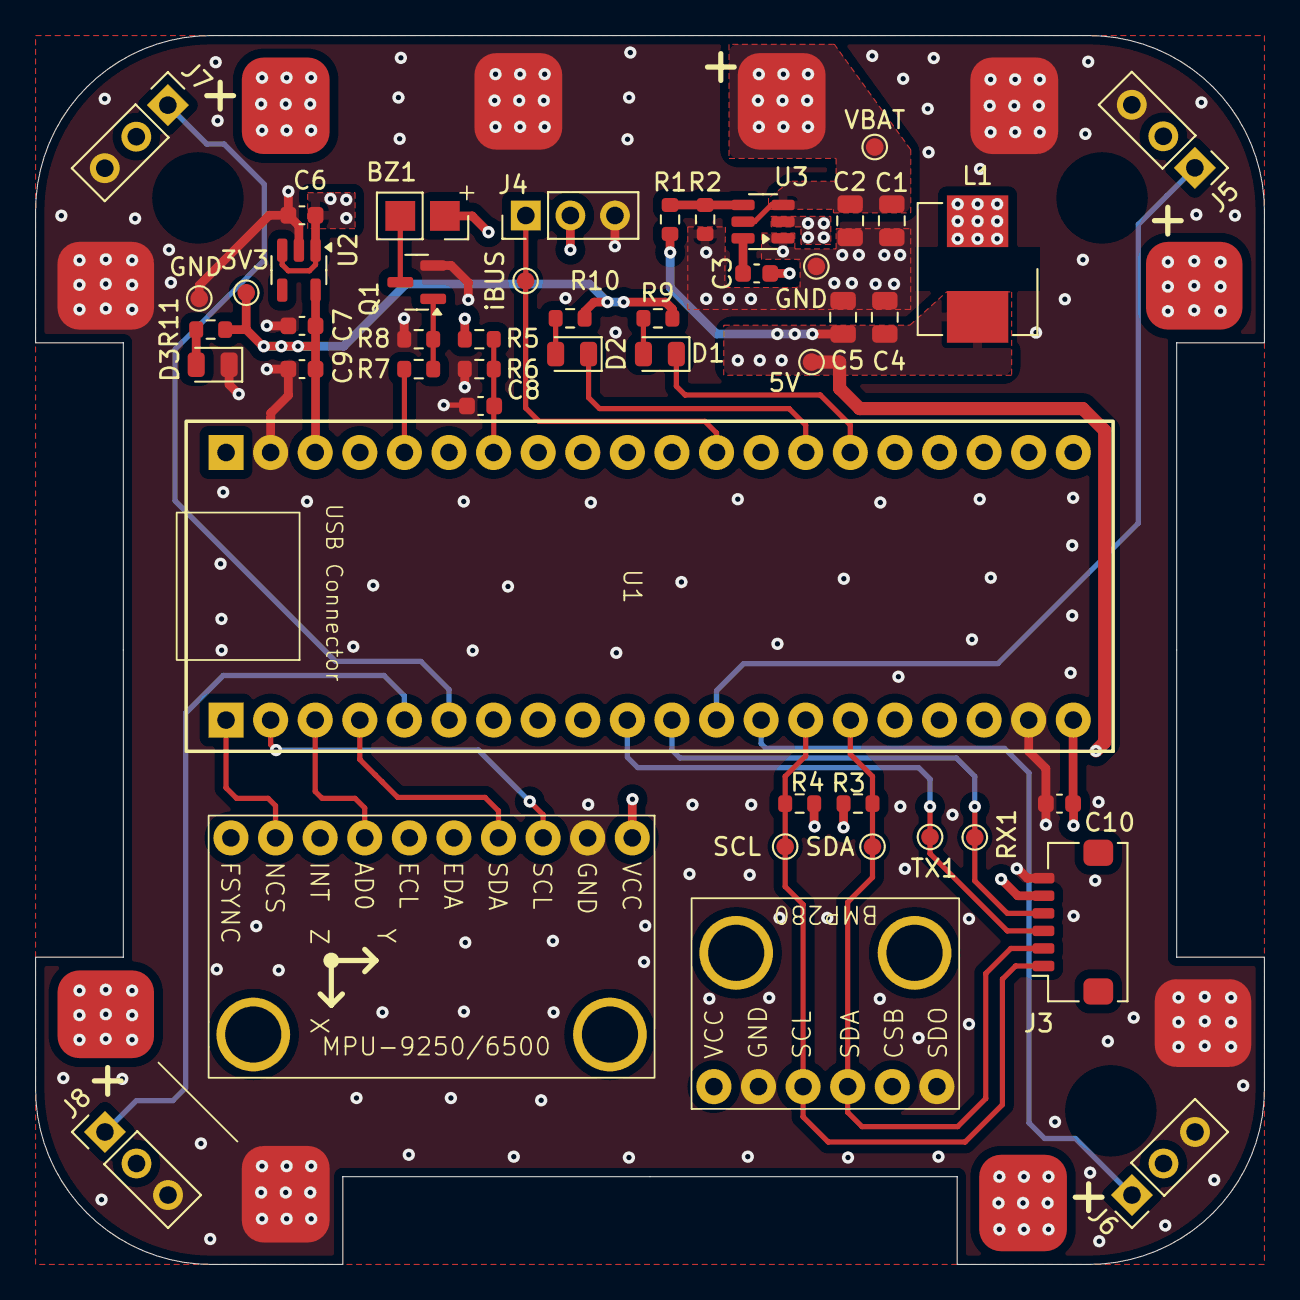
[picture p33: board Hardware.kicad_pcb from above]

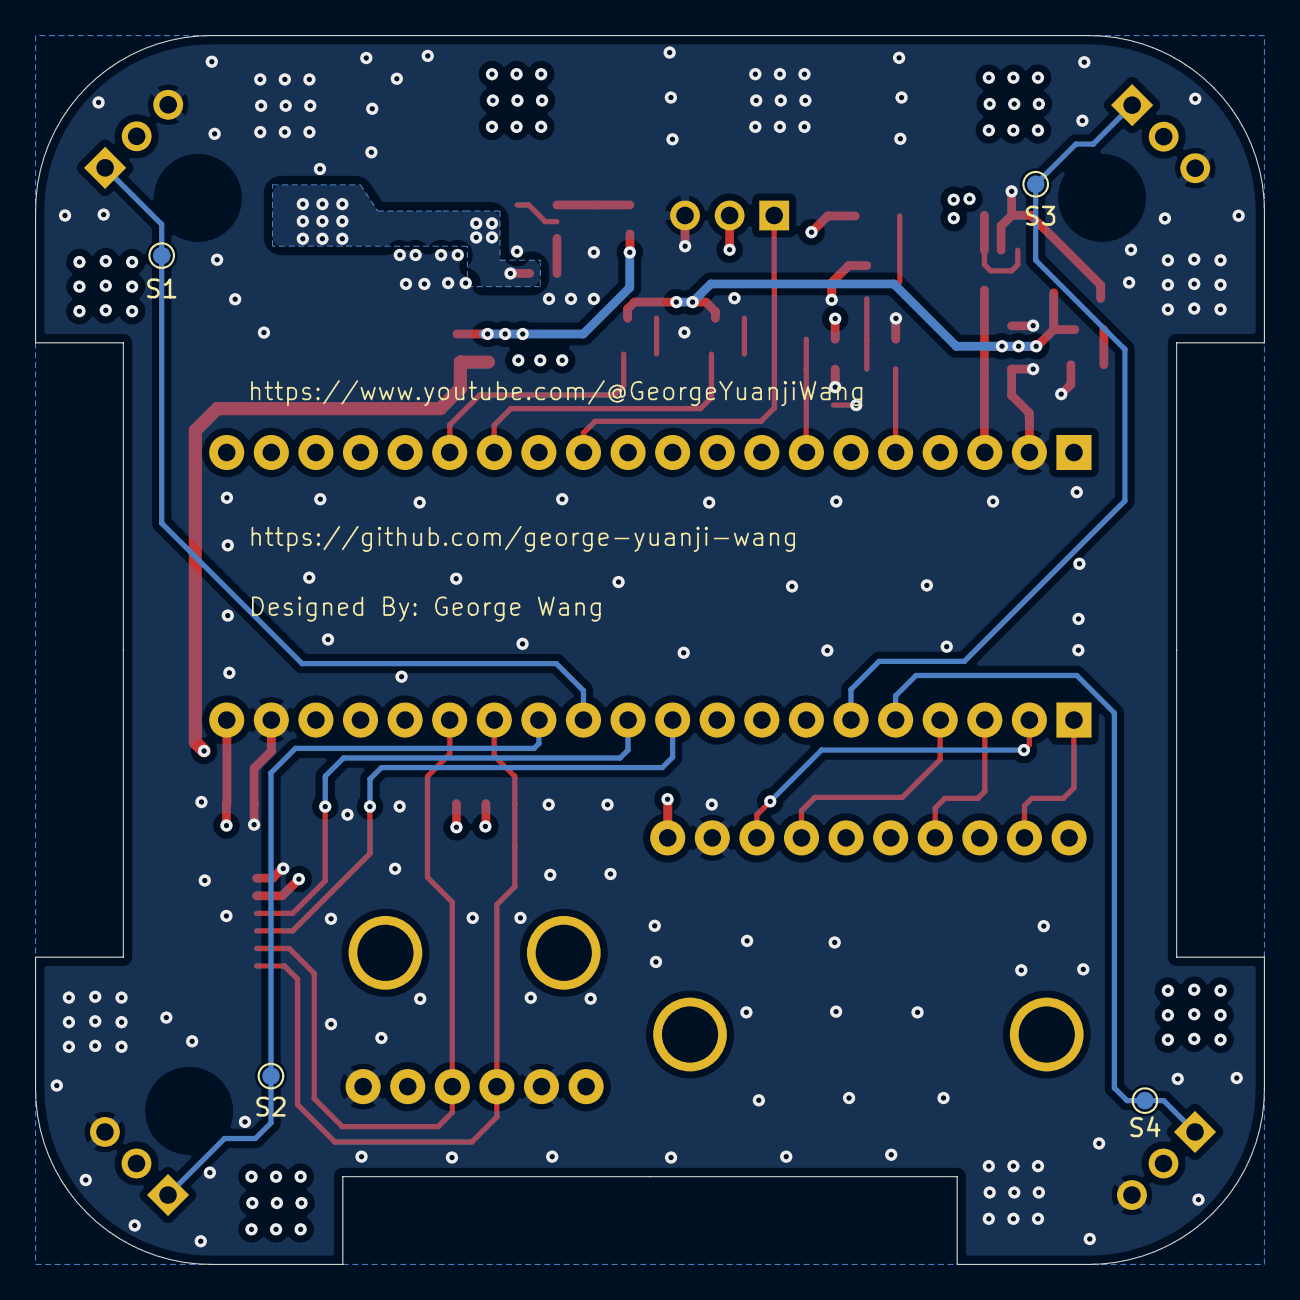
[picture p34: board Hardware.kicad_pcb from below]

Board: 4 copper layers, 70.0 x 70.0 mm, 57 parts (4 on the bottom side), 29 nets.

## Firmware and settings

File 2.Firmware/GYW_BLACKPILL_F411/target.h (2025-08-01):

#pragma once

#define TARGET_BOARD_IDENTIFIER "GYW_BLACKPILL_F411"
#define USBD_PRODUCT_STRING    "GYW_BLACKPILL_F411"

//LEDs
//#define LED0  PC13 
#define LED0 PA0
#define LED0_INVERTED        
#define LED1   PA1
#define LED1_INVERTED       

#define USE_BUZZER
#define BEEPER PB2 
#define BEEPER_INVERTED      

// *************** SPI2 for MPU9250/MPU6500 **********************
#define USE_SPI
#define USE_SPI_DEVICE_2

#define SPI2_SCK_PIN   PB13
#define SPI2_MISO_PIN  PB14
#define SPI2_MOSI_PIN  PB15

//uncomment this block for MPU9250
/*  
#define USE_IMU_MPU9250
#define IMU_MPU9250_ALIGN   CW0_DEG
#define MPU9250_CS_PIN      PB12
#define MPU9250_SPI_BUS     BUS_SPI2
*/

//comment out this block for MPU9250
#define USE_IMU_MPU6500
#define IMU_MPU6500_ALIGN   CW0_DEG
#define MPU6500_CS_PIN      PB12
#define MPU6500_SPI_BUS     BUS_SPI2


// *************** UART *****************************
#define USE_VCP                

#define USE_UART1                         //GPS port
#define UART1_TX_PIN   PA15
#define UART1_RX_PIN   PB3

#define USE_UART2                         //SBUS RC
#define UART2_TX_PIN   PA2                
#define UART2_RX_PIN   PA3

#define SERIAL_PORT_COUNT  3              

#define DEFAULT_RX_TYPE    RX_TYPE_SERIAL
#define SERIALRX_PROVIDER  SERIALRX_SBUS
#define SERIALRX_UART      SERIAL_PORT_USART2

//*************** I2C1 for Baro & Mag ******************
#define USE_I2C
#define USE_I2C_DEVICE_1
#define I2C1_SCL                PB6
#define I2C1_SDA                PB7
#define DEFAULT_I2C_BUS         BUS_I2C1

#define USE_BARO
#define BARO_I2C_BUS            BUS_I2C1
#define USE_BARO_BMP280

#define USE_MAG
#define MAG_I2C_BUS             BUS_I2C1
#define USE_MAG_QMC5883

//*************** ADC (VBAT) *****************************
#define USE_ADC       
#define ADC_INSTANCE            ADC1
#define ADC1_DMA_STREAM         DMA2_Stream0

#define ADC_CHANNEL_1_PIN       PB0

#define VBAT_ADC_CHANNEL        ADC_CHN_1

//***************  OTHERS *************************
#define DEFAULT_FEATURES  ( FEATURE_TX_PROF_SEL | FEATURE_VBAT)

#define TARGET_IO_PORTA  0xffff
#define TARGET_IO_PORTB  0xffff
#define TARGET_IO_PORTC  0xffff
#define TARGET_IO_PORTD  (BIT(2))

#define MAX_PWM_OUTPUT_PORTS  4

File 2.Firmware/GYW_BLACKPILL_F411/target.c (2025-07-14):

/*
* This file is part of Cleanflight.
*
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
* You should have received a copy of the GNU General Public License
* along with Cleanflight.  If not, see <http://www.gnu.org/licenses/>.
*/

#include <stdbool.h>
#include <platform.h>
#include "drivers/bus.h"
#include "drivers/io.h"
#include "drivers/pwm_mapping.h"
#include "drivers/timer.h"
#include "drivers/pinio.h"

timerHardware_t timerHardware[] = {
    //Motor 1 -> PA9
    DEF_TIM(TIM1, CH2, PA9,  TIM_USE_MC_MOTOR, 0, 1),
    //Motor 2 -> PA8 
    DEF_TIM(TIM1, CH1, PA8,  TIM_USE_MC_MOTOR, 0, 1),
    //Motor 3 -> PB4
    DEF_TIM(TIM3, CH1, PB4,  TIM_USE_MC_MOTOR, 0, 0),
    //Motor 4 -> PB5
    DEF_TIM(TIM3, CH2, PB5,  TIM_USE_MC_MOTOR, 0, 0),
};

    

const int timerHardwareCount = sizeof(timerHardware) / sizeof(timerHardware[0]);

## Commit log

2025-07-14 Mechanical Parts
    [Battery_Plate v2.step, Bottom_Plate v4.step, arm_plate_1 v17.step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]
2025-07-15 Create Screenshot 2025-07-15 at 12.45.55 PM.png
2025-08-01 almost done readme
    documentations missing inav config procedures
    [Battery_Plate v2.step, Battery_Plate v3.step, Bottom_Plate v4.step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]
2025-08-13 mf files
    [ABS_print.3mf, All_on_one_plate.3mf, CF_prints.3mf]

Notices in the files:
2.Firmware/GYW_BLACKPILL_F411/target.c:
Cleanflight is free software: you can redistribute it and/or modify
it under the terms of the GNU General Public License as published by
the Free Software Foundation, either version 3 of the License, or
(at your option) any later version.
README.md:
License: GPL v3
